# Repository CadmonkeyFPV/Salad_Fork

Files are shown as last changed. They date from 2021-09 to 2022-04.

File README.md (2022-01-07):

# Salad Fork

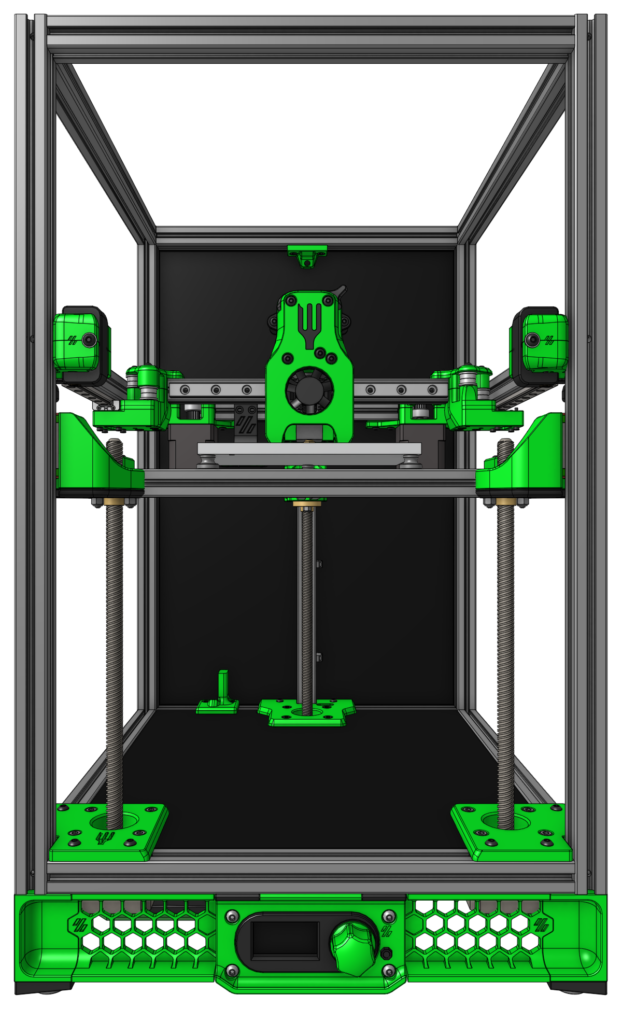
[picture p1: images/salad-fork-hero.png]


The Salad Fork is a [Voron Trident][tridentURL] scaled down to use 1515 aluminum extrusions for the frame instead of 2020, exactly [like how the Micron][micronURL] is a [Voron 2.4][v2URL] scaled down. It is not a modification for a Voron V0, but a from-scratch build that requires longer extrusions and rails, two more V0.1 integrated-leadscrew Z motors, a higher-wattage power supply, possibly a bigger bed…

Why go to the trouble of a whole new build? Well, Salad Fork features:

- Support for build volumes of 120mm³ or 150mm³ (1.95× the build volume of a V0.1!)
- [Klicky support][klickyURL]
- [Purge bucket support][purgeBucketURL]

Coming soon™…

- [Sexbolt support][sexboltURL]
- Magnetically-attached panels

[tridentURL]: https://vorondesign.com/voron_trident
[micronURL]: https://github.com/hartk1213/micron
[v2URL]: https://vorondesign.com/voron2.4
[klickyURL]: https://github.com/jlas1/Klicky-Probe
[purgeBucketURL]: https://github.com/CadmonkeyFPV/Salad_Fork/tree/master/MODS/Dishwasher
[sexboltURL]: https://github.com/hartk1213/MISC/tree/main/Voron%20Mods/Voron%202/2.4/Voron2.4_SexBolt_ZEndstop

# BOM

[The latest official BOM is available on Google Sheets](https://docs.google.com/spreadsheets/d/1IUI6oiu36kkzXx5OPMRfrHjvIH2P_M3332lTih6h6LI/edit#gid=1896851909). The information below may not be complete; last updated November 17, 2021.

<details>
    <summary>
    Frame (120mm³ build volume)
    </summary>

Component | Quantity | Notes
--- | :-: | ---
HFS3-1515-400 | 4 | Cross-drill 7.5mm from both ends, plus drill 1× gantry hole each per drill guide
HFS3-1515-270 | 6 | Tap both ends
HFS3-1515-240 | 5 | Tap both ends, cross-drill 2 extrusions at center
HFS3-1515-230 | 1 | Tap one end
HFS3-1515-210 | 1 |
HFS3-1515-145 | 1 |
HFS3-1515-140 | 1 | Tap one end
</details>

<details>
    <summary>
    Frame (150mm³ build volume)
    </summary>

Component | Quantity | Notes
--- | :-: | ---
HFS3-1515-400 | 4 | Cross-drill 7.5mm from both ends, plus drill 1× gantry hole each per drill guide
HFS3-1515-300 | 6 | Tap both ends
HFS3-1515-270 | 5 | Tap both ends, cross-drill 2 extrusions at center
HSF3-1515-240 | 1 | Tap one end
HSF3-1515-230 | 1 |
HFS3-1515-175 | 1 |
HSF3-1515-170 | 1 | Tap one end
</details>

<details>
    <summary>
    Fasteners
    </summary>

Component | Quantity
--- | :-:
M2x6 BHCS | 24
M2x10 self-tapping | 4
M2x12 SHCS | 8
M3x6 BHCS | 49
M3x6 SHCS | 10
M3x8 BHCS | 41
M3x8 SHCS | 8
M3x10 BHCS | 40
M3x12 BHCS | 4
M3x12 SHCS | 18
M3x16 SHCS | 3
M3x20 SHCS | 6
M3x25 BHCS | 18
M3x25 SHCS | 6
M3x30 BHCS | 2
M3x35 BHCS | 5
M3x35 SHCS | 4
M5x16 BHCS | 3
M3 Heatset | 30
M3 Washer | 26
M3 lock nut | 6
M3 hex nut | 98
M4 knurled nut | 3
M5 hex nut | 3 
6x3 neodymium magnet | 8
</details>

<details>
    <summary>
    Motion
    </summary>

Component | Quantity
--- | :-:
NEMA14 stepper | 2
NEMA17 integrated-leadscrew stepper | 3
MGN9C 180 | 1 (for 120mm³)
MGN7H 200 | 5 (for 120mm³)
MGN9C 210 | 1 (for 150mm³)
MGN7H 230 | 2 (for 150mm³)
MGN7H 200 | 3 (for 150mm³)
Gates GT2 6mm open belt | 4m
F623-RS flanged bearings | 24
GE5C spherical bearings | 3
D2F switch | 4
TR8×8 leadscrew nut | 3
Rubber foot | 4
</details>

<details>
    <summary>
    Electronics
    </summary>

Component | Quantity | Notes
--- | :-: | ---
Control board | 1 | Fysetc Spider or BigTreeTech Octopus
TMC 2209 driver | 6 |
Raspberry Pi | 1 | The Klipper host
C13 power cable | 1 | 
Meanwell UHP-200-24 | 1 |
Keenovo 100mm² 60W 24V heater | 1 | DC bed heater, 120mm³ build
Keenovo 120mm² 120W 24V heater | 1 | DC bed heater, 150mm³ build
Keenovo 100mm² 60W 120/240V heater | 1 | AC bed heater, 120mm³ build
Keenovo 120mm² 120W 120/240V heater | 1 | AC bed heater, 150mm³ build
AC SSR (Omron G3NA-210B-UTU DC5-24, Panasonic AQA211VL) | 1 | for AC bed heater
</details>

<details>
    <summary>
    Toolhead
    </summary>

Component | Quantity | Notes
--- | :-: | ---
NEMA14 pancake stepper | 1 |
BMG gear set | 1 |
3010 axial fan | 1 | Only for Dragonfly BMS hotend
3007 axial fan | 1 | All other hotends
3010 blower fan | 2 |
Hotend | 1 |
</details>

# Salad Fork in action

Salad Fork video from CadmonkeyFPV (https://youtu.be/ibptF2t73A4)

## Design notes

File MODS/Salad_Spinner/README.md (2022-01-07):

# The Salad Spinner Spool Holder

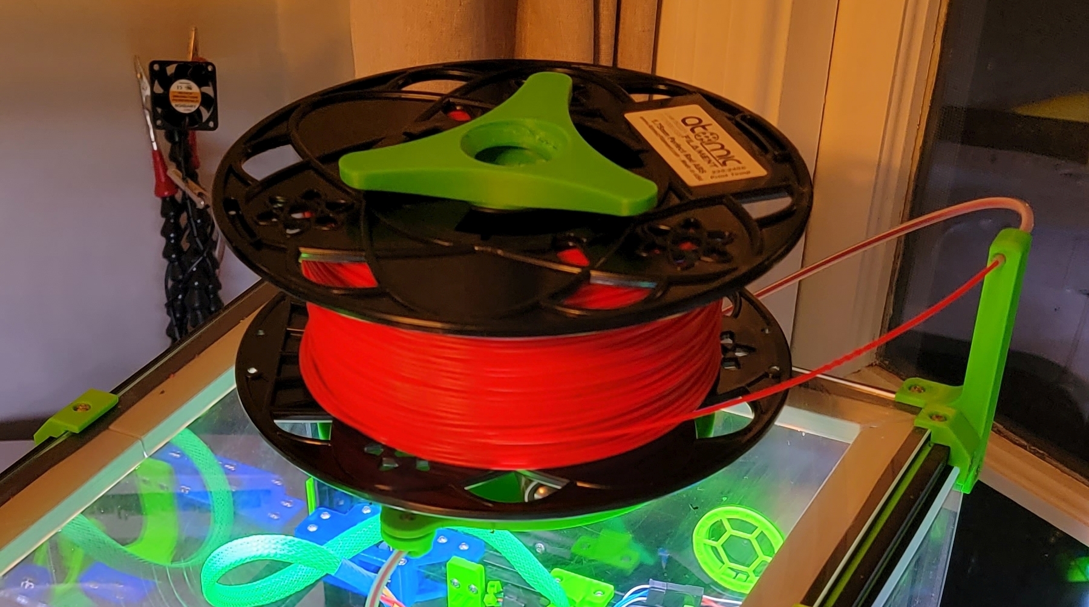
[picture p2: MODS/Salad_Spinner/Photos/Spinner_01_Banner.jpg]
The Salad Spinner


Horizontal Spool Holder designed for the Salad Fork project but adaptable to many other printers.

Intended to mount to top panel of printer. Stand alone turntable for use on other platforms.

Threaded clamps for 1kg and 5 pound spools (5 pound version has only been tested on KVP 5 pound spool at this time) and a clamp for thinner spools (0.25 kg SainSmart TPU for example)

Turntable gets mounted to top panel of printer. Rectangular boss achors to rear of printer and riser couples that to extrusion using M3x12 BHCS and preloaded hex nut. Adjust riser Z dimension in slicer to accomodate different panel and foam combinations, STL as provided works with 3mm panel, 6mm foam compressed to 5mm. The front ear on the turntable requires the top panel to be drilled to accept an M3, and the Bowden guide (with heat set installed) mounts to the interior of the printer on this bolt. Guide loosely secures the Bowden mid span. You will need to experiment with overall bowden length to determine was works best for your toolhead and other accessories/mods. I have enough Bowden to extend 4" past the front panel when stretched out, which coils down to the Orbiter I am running.

Standalone Turntable uses (3) M3 BHCS sized to work with your panel thickness.

Spinner core gets M5 heat set inserts in each leg. Follow that with a flat washer or shim against the body, one bearing and finally secure with an M5x12 BHCS. Repeat 2 more times for each leg.

Corner Clip Bowden support mounts replaces the top panel corner mount and supports the spool end of the reverse Bowden tube at approx middle of the spool. Bowden is a tight fit, use a rat tail file if you need to open up bore to get the tube in place. There is a bend in the bore to help hold this tight.

## BOM - Per spinner Core

- (3) M5x12 BHCS (SHCS should work as well)
- (3) M5 Heat Set Inserts [Amazon](https://www.amazon.com/gp/product/B07NBSWBQ8)
- (3) M5 flat washers or 5mm x 1mm shims
- (3) 625 bearings - any variant can be used - RS, ZZ, etc

## BOM - Turntable Salad Fork w/ 3mm acrylic top panel

- (1) M3x8 BHCS 
- (1) M3x12 BHCS (or M3x10)
- (1) M3 Hex Nut
- (1) M3 Short Heat Set Insert (Voron Standard)

### OPTIONAL BOM - Bowden BPST - Secures Bowden tube where it passes through rear panel into the print cavity

- (1) Pass through Bowden BPST fitting

### OPTIONAL BOM - Turntable Standalone - For use on other printers (I'm using on a V2.4)

- (3) M3 BHCS - Length appropriate for panel thickness

#### Coming Soon - "Top Hat" style 1515 extrusion based cover for Salad Forks

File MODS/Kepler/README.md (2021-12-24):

# Kepler Tool Head

Derived from the Micron and Mini-Afterburner Tool Heads

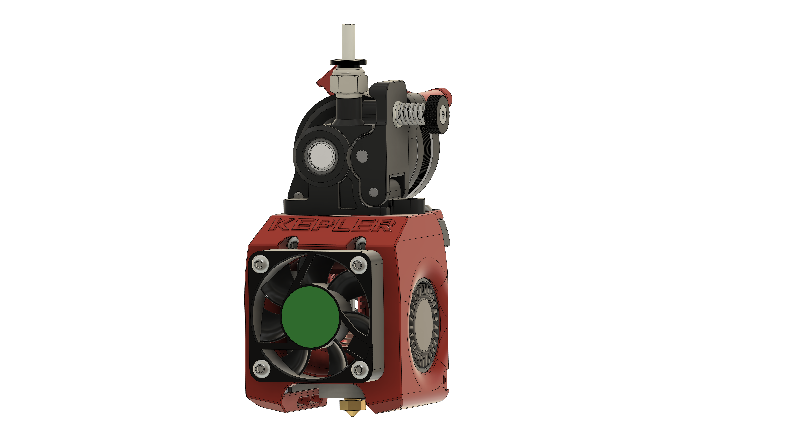
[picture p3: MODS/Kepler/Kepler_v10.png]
Kepler


# Use at your own risk - this is still a work in progress.

I'm running this on a Salad Fork build. Better overhang results and extrusion consistency so far as compared to the Micron toolhead.

This only supports the Dragon Hot End at this time

## BOM

- (1) Orbiter v1.5
- (1) Dragon Hot End - Standard or Hi-Flow variants
- (1) Pancake Stepper Toolhead PCB
- (2) 4010 Radial Fans - whatever voltage you prefer
- (1) 4010 Axial Fan - whatever voltage you prefer
- (4) M3x10 BHCS Hot End Fan
- (4) M3 Hexnuts Hot End Fan
- (2) M3x35 SHCS Main Mounting Screws
- (1) M3x6 3rd Mounting Point
- (4) M3x8 BHCS Carriage Mount
- (2) M3x20 SHCS Klicky Mount
- (2) M3x10 BHCS Blower Anchors (optional?)
- (2) M3x10 BHCS Orbiter Mount
- (2) M3x6 PCB Anchors
- (4) M2.5x?? The Dragon Screws for a v0
- Zip Ties to keep it neat

Assembly Tips:
- Remove the upper ears on the 4010 Radials
- Insert the (2) M3x35 SHCS before installing the Hot End Fan
- Route the Hot End Fan wires down and through the fan hole, merge with the 4010 Radial Fan through the nut channel
- Assemble the Hot End Fan before the Radials, the nuts will be mostly captivated once the 4010 Radials are inserted
- Be mindful of the wires - the loops are enough for the part fans, thermocouple, and Hot End Fan.
- Heater wires hang loose at this stage, zip tie to the secured fan wires to keep them from dangling

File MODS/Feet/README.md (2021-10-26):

# TPU Feet

Alternate feet for the Salad Fork

Foot Model

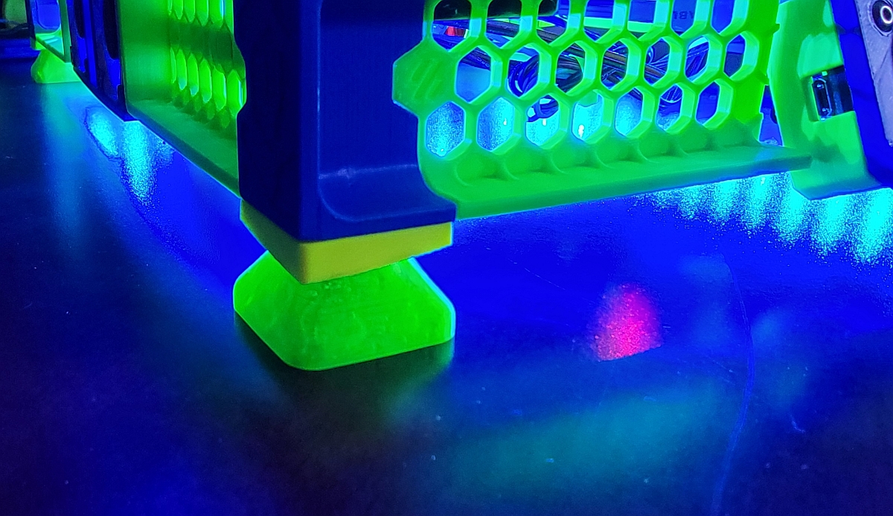
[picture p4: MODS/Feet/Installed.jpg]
Installed


Print in TPU - Low wall count ~2 and minimal infill ~10% gyroid worked well for me to yield a supple foot with some vibration isolation, 5 top/bottom layers

## BOM
- (4) M3x10 SHCS

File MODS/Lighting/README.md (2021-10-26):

# Light Bar Mounts 

For 12mm wide LED strips

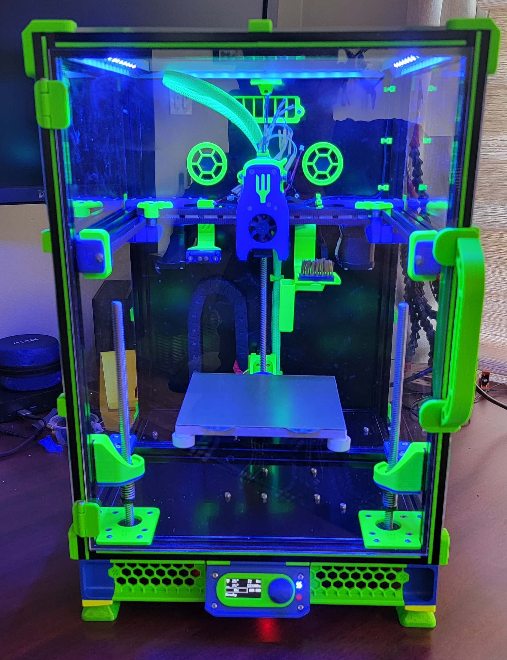
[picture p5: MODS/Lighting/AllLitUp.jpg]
All Liut Up


Print sections per your frame size. Parametric Fusion360 file provided to customize lengths

## BOM

- (2) M3x6 BHCS per segment
- (2) M3 Hexnuts per segment
- 12mm wide (or less) LED strip

Assembly is straightforward.

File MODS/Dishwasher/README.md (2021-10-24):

# The "Dishwasher" Nozzle Scrubber and Purge Bucket

Nozzle scrubber and purge bucket designed for the Salad Fork project.

Bolts to underside of rear 1515 extrusion, adjacent to A Drive

Spacing based on Mini-Afterburner with Dragon Hotend

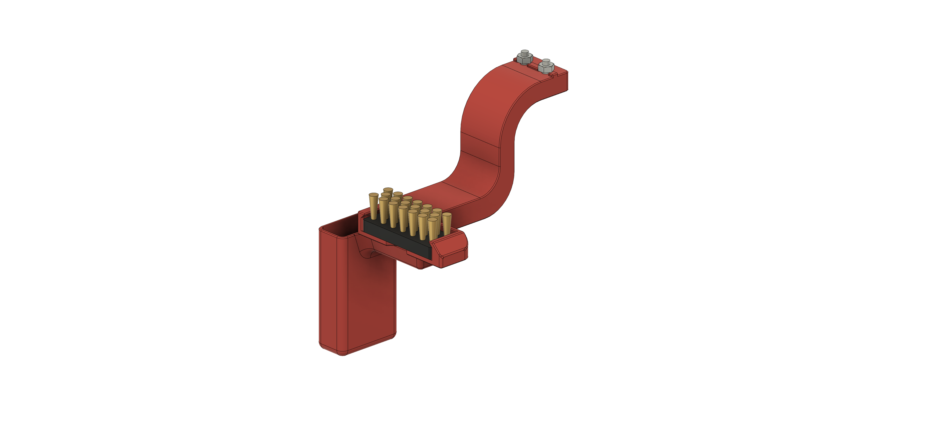
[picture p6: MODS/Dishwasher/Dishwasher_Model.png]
The Dishwasher

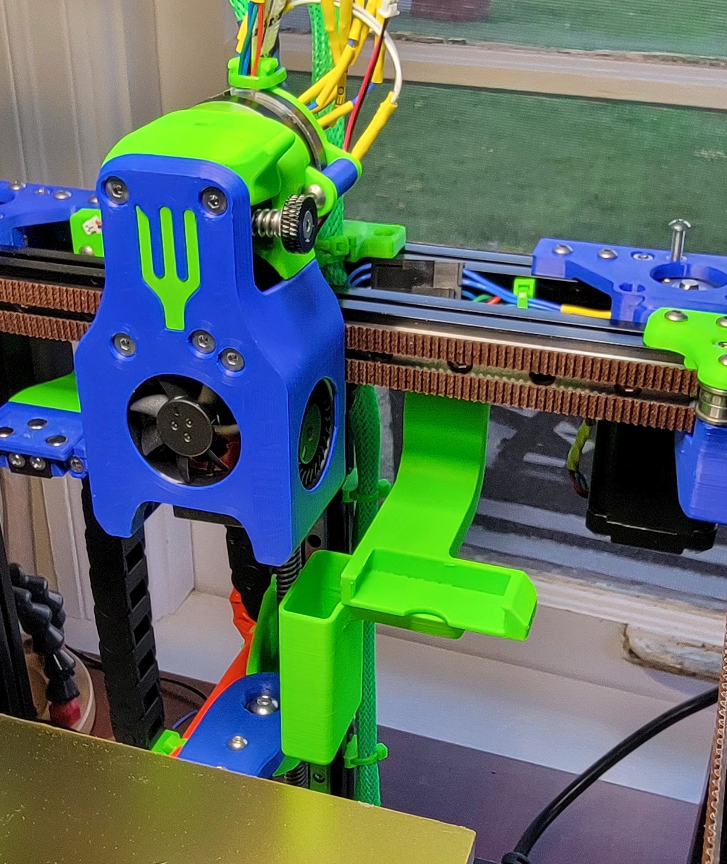
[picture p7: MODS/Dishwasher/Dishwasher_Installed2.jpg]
Installed


## BOM

- (2) M3x10 SHCS
- (2) M3 Hexnuts
- (6) 6x3 Magnets
- (1) Brass Mini-Brush (cut head off)

Brush overall height (head & bristles) should be roughly 15mm

Assembly is straightforward.

20211023 - Additional STL for +8mm drop on the mount to accomodate longer bristles of Home Depot brushes

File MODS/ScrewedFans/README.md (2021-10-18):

# Fan Supports with M3 Screw Tabs

Upgraded fan support for the Salad Fork project. 

Provides tabs to screw the 4010 electronics bay fans in place. M3 SHCS threads into the plastic, no heat set required.

The Dishwasher
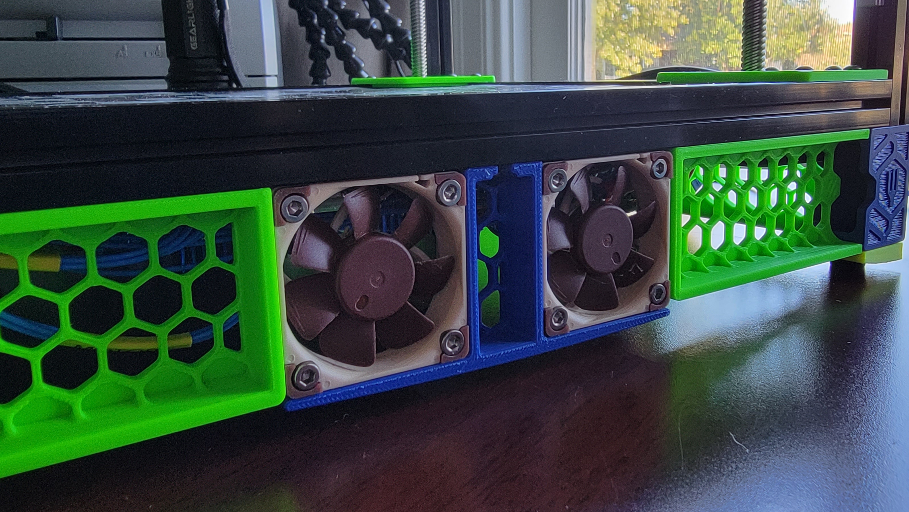
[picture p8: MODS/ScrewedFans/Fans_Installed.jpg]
Installed


## BOM

- (6) M3x12 SHCS
- (2) 4010 Fans (I prefer Noctua for whisper quiet silence)
- (1) M3x6 BHCS (to mount to extrusion if you don't already have)
- (1) M3 Hex Nut (ditto)

Press firmly as you thread the screws in so they form some amount of thread instead of just cutting plastic out of the way.

I added (2) additional M3x12 w/ hexnuts in the unsupported corner just for aesthetics. They aren't required though.

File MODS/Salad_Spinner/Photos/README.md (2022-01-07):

# The Salad Spinner Spool Holder

### Overview
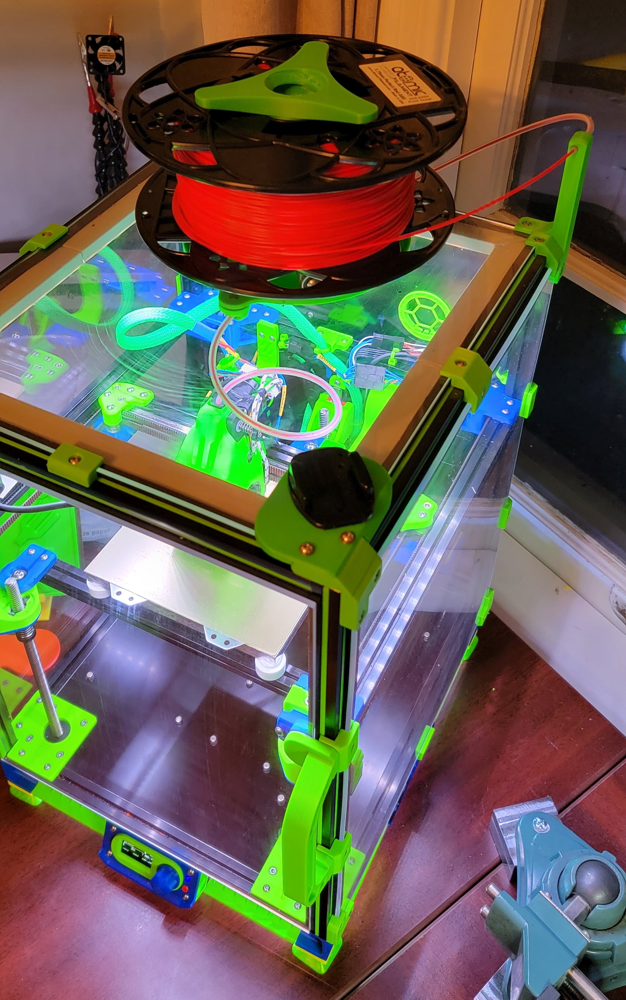
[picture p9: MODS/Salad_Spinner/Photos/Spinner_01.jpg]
Overview


### Turntable
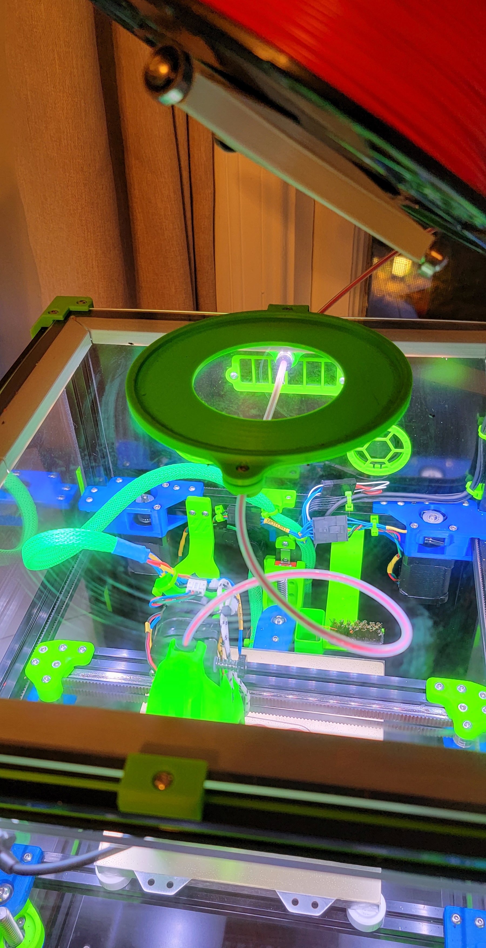
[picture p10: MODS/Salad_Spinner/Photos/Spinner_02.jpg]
Turntable


### Bowden Routing
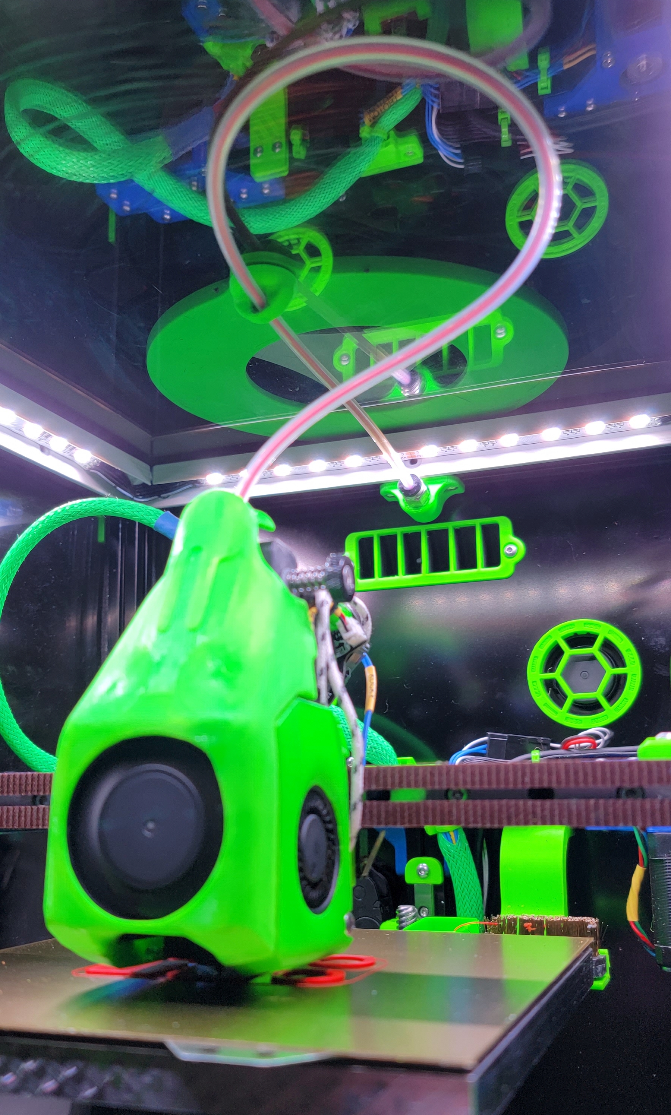
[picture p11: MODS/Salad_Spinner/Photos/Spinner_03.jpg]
Bowden


### Stable of Spinners
Stable

### Spinner Detail 1
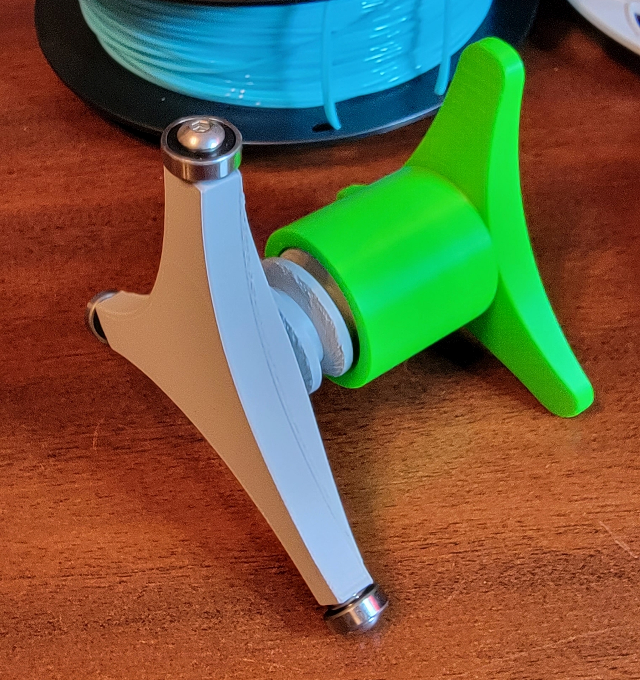
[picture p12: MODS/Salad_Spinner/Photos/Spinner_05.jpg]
Detail1


### Spinner Detail 2
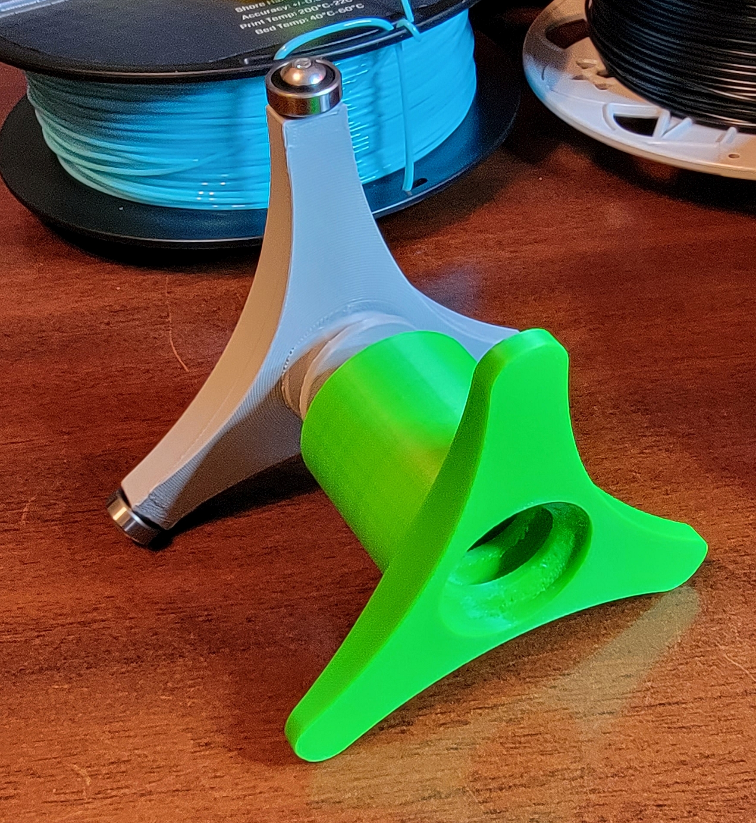
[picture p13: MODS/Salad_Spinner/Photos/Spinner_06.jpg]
Detail2


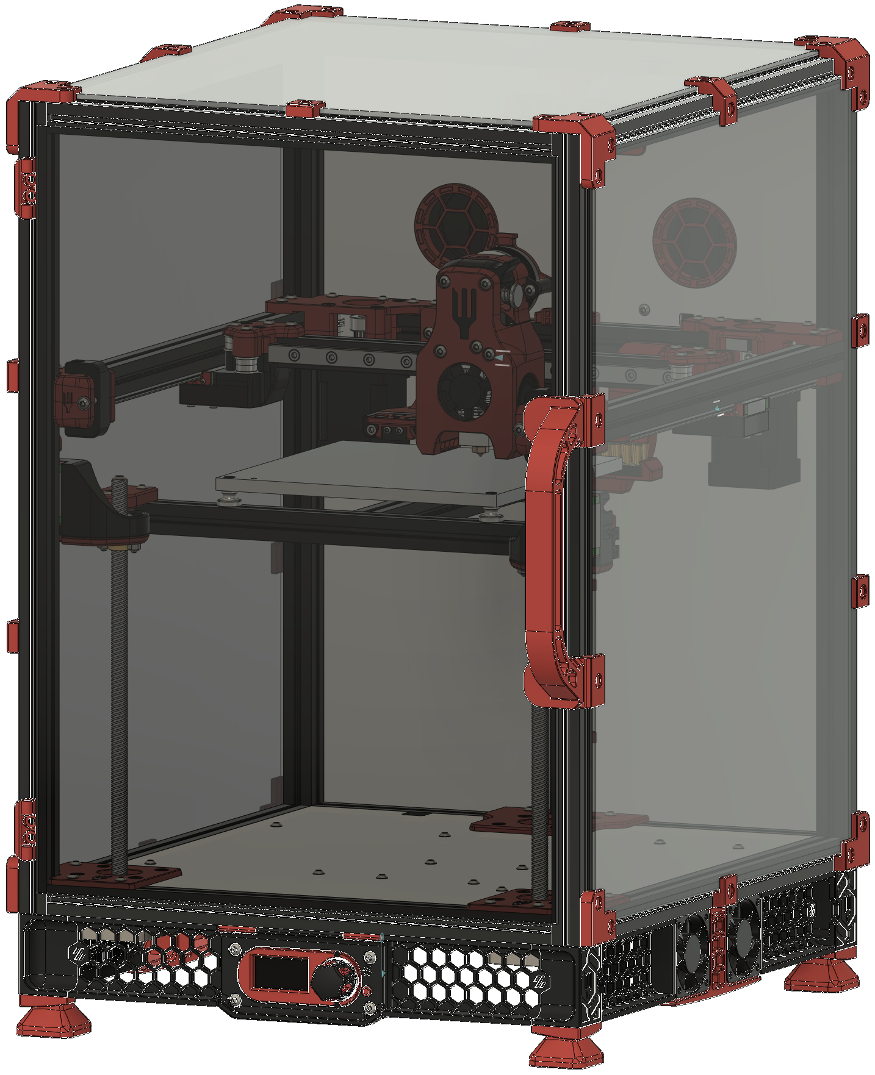
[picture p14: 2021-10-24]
Images/SF_Assy_20190919_v21.png

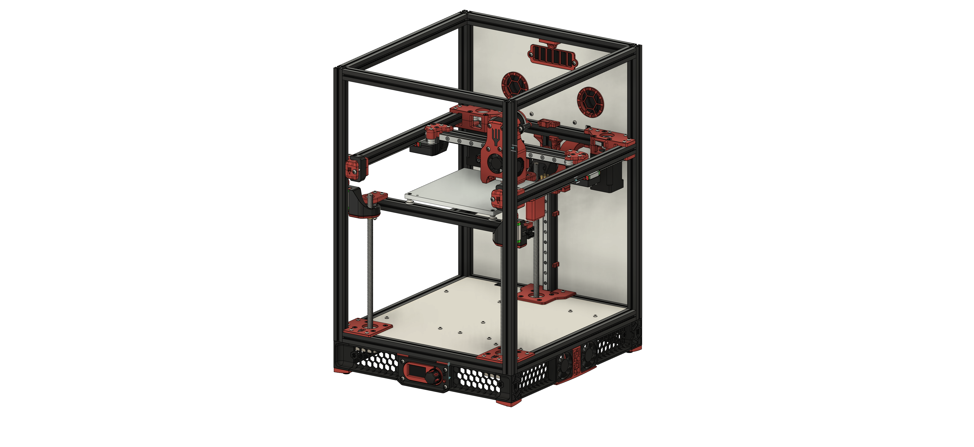
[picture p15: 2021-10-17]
Images/Salad_Fork_CADMonkeyFPV.png

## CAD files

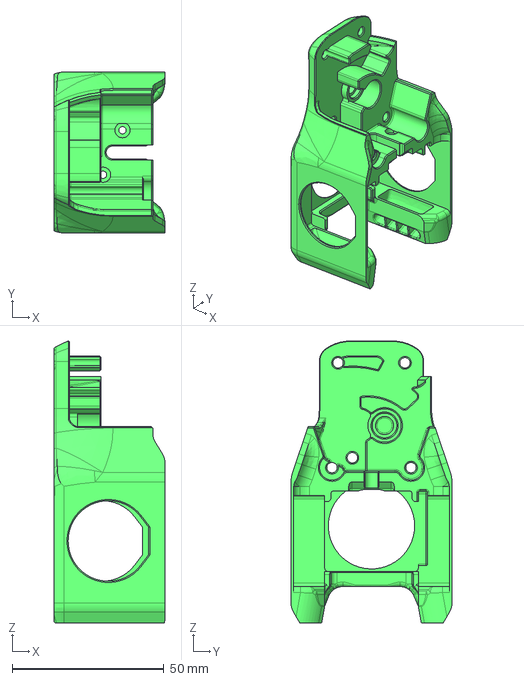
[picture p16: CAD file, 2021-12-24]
CAD/Cowling_Dragonfly_BMO.step
36.5 x 53.0 x 92.8 mm

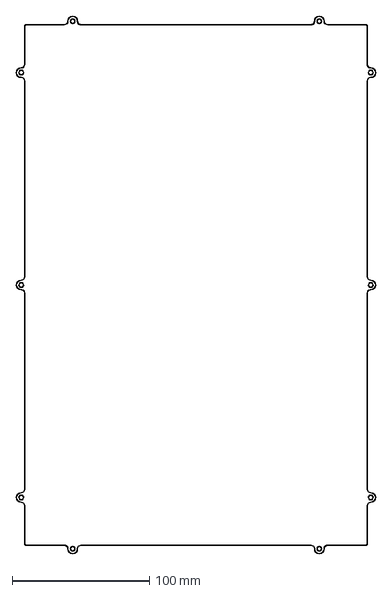
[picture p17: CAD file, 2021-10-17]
DXF/120/back.dxf
262.0 x 391.9 mm

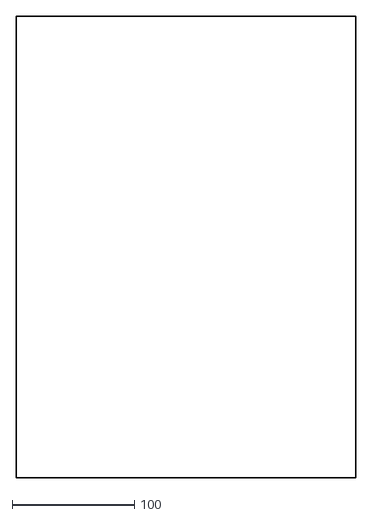
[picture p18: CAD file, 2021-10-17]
DXF/CADMonkeys_DXFs/ACRYLIC_FRONT_CLEAR_x1.dxf
278.0 x 378.0

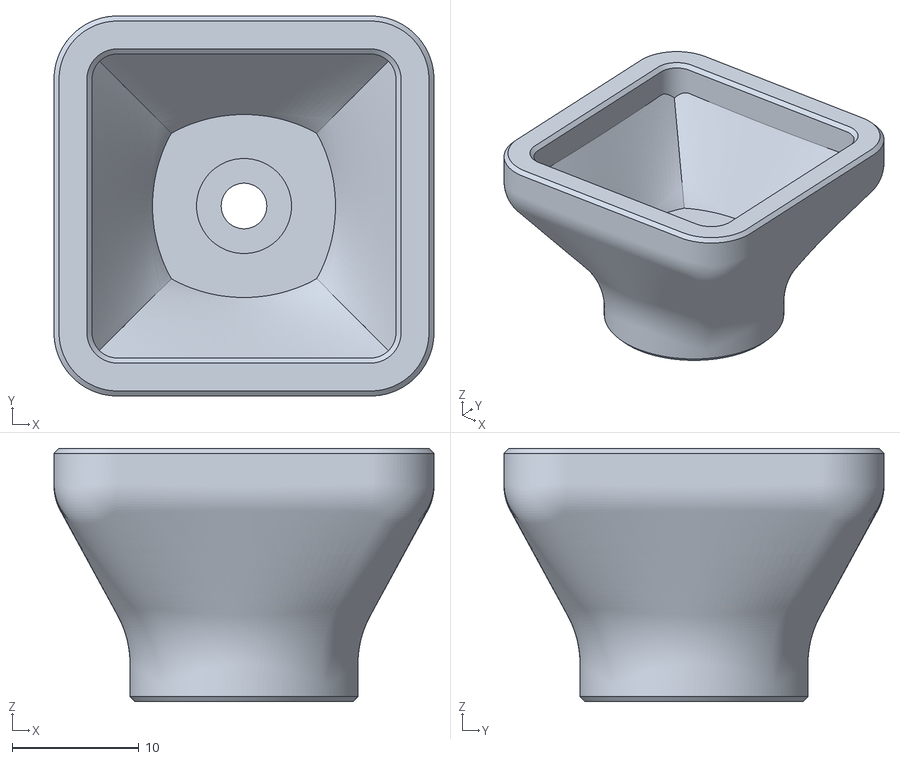
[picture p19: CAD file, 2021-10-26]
MODS/Feet/[a]_TPU_Foot_x4.stl
30.0 x 30.0 x 20.0

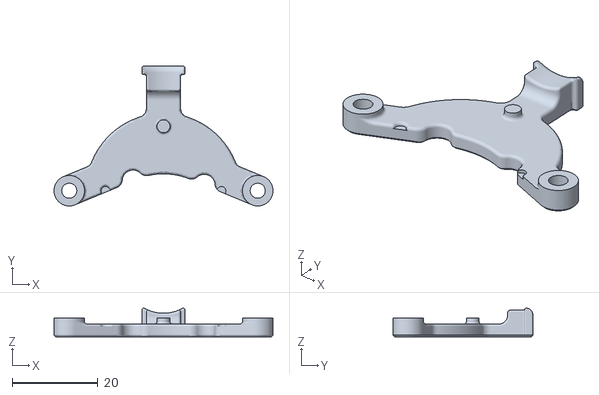
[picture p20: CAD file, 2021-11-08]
MODS/Kepler/Kepler_Strain_Relief_v3.stl
50.9 x 32.5 x 6.69

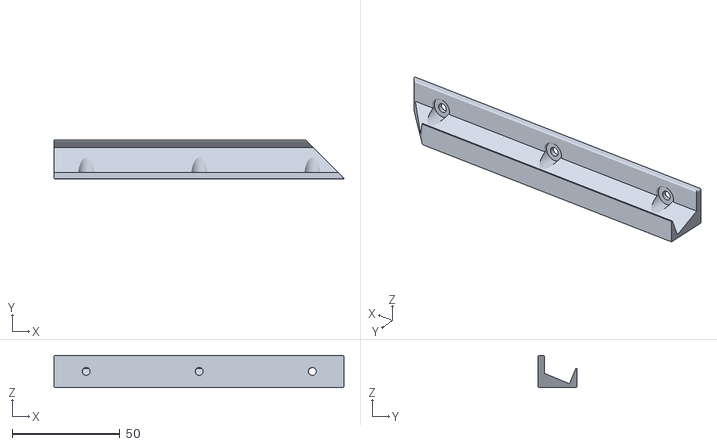
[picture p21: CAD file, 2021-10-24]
MODS/Lighting/LightBar_135B_v1.stl
134.6 x 18.0 x 15.0

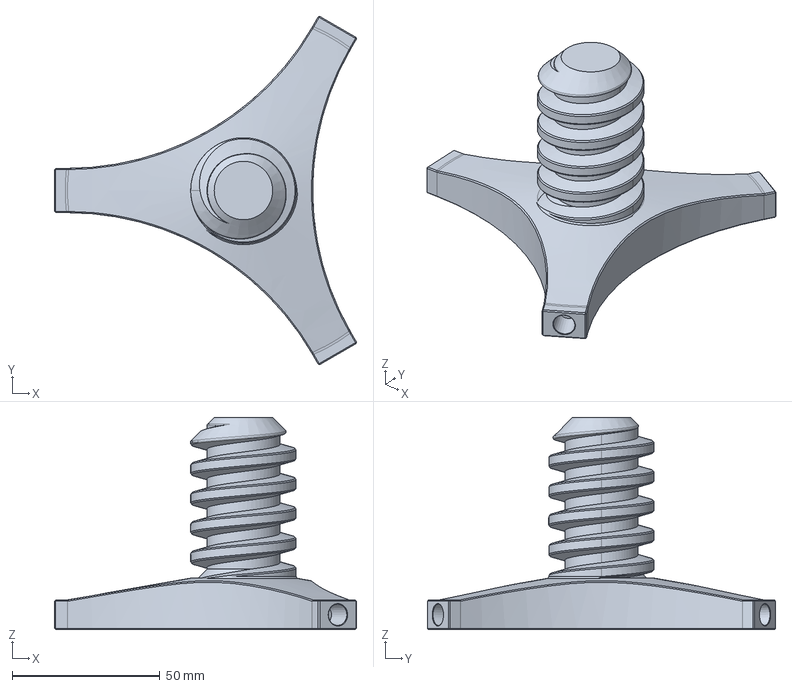
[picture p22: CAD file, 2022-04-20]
MODS/Salad_Spinner/CAD/Filament_Spinner_7.1ODInserts.step
102.3 x 118.0 x 71.9 mm

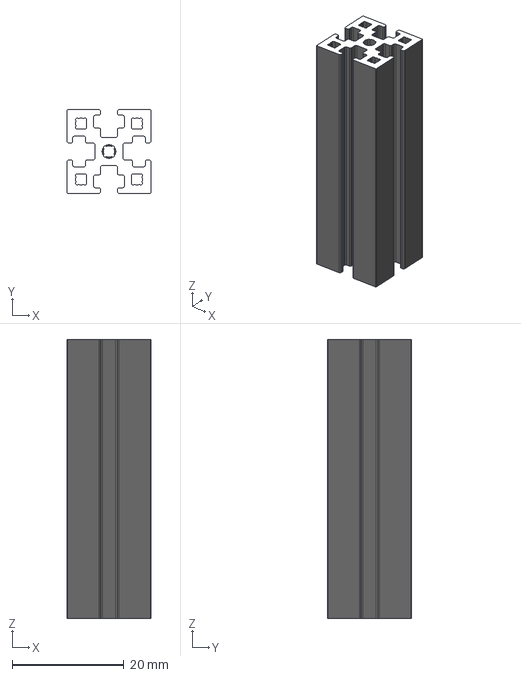
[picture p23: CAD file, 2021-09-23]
References/MakerBeam1515.stp
15.0 x 15.0 x 50.0 mm

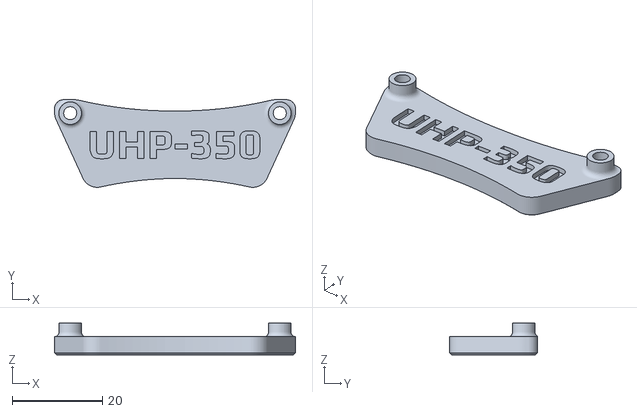
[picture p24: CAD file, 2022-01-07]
STL/Electronics/UHP-350_bracket_x2.stl
53.4 x 19.4 x 7.00

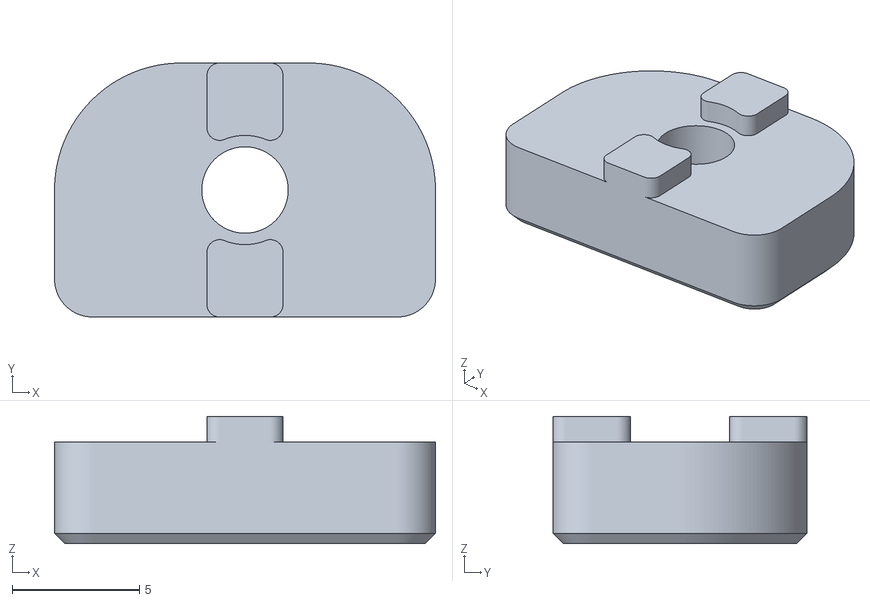
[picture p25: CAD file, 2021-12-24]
STL/Frame/[a]_railstop_x5.stl
15.0 x 10.0 x 5.00

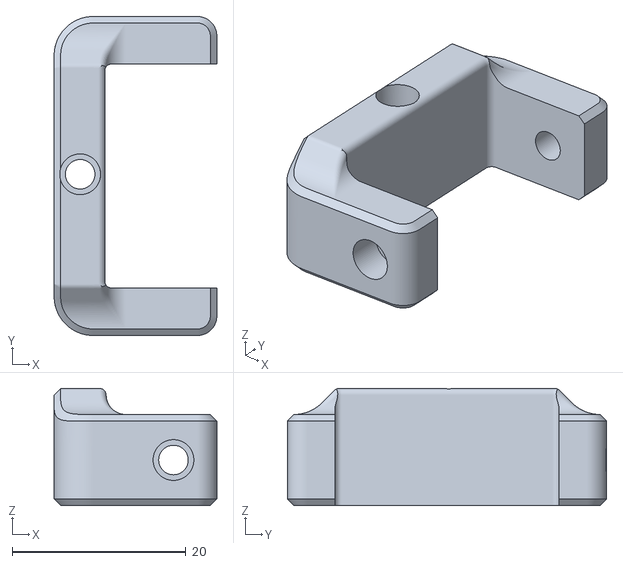
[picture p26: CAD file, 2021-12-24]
STL/Gantry/[a]_tensioner_b_x1.stl
18.8 x 36.8 x 13.5

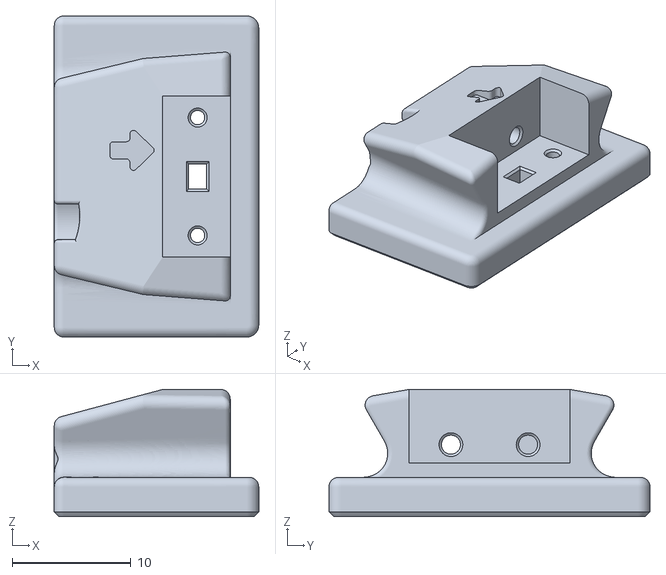
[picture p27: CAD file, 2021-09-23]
STL/Klicky/probe_body_x1.stl
17.2 x 27.0 x 10.7

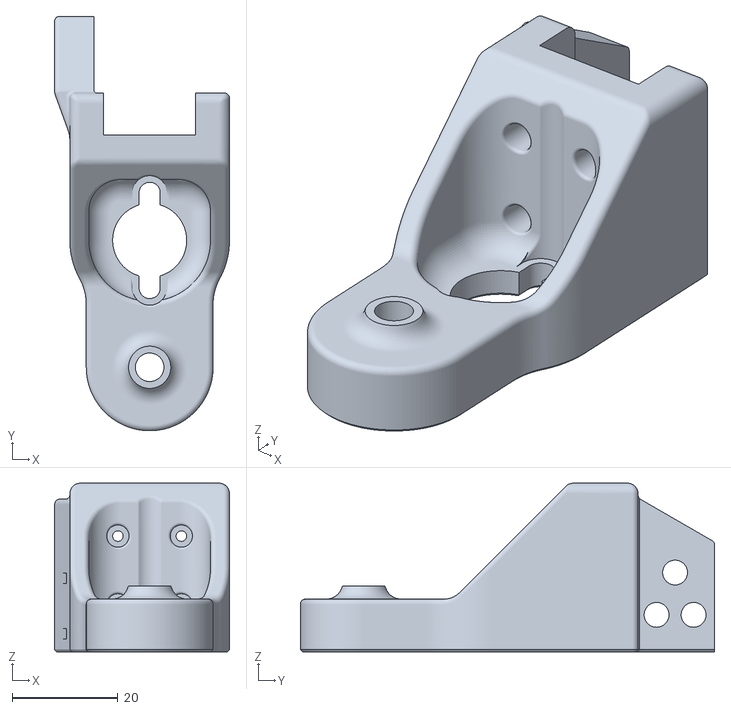
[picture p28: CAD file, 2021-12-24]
STL/Motion/z_carriage_rear_3hole_x1.stl
33.1 x 78.4 x 31.9

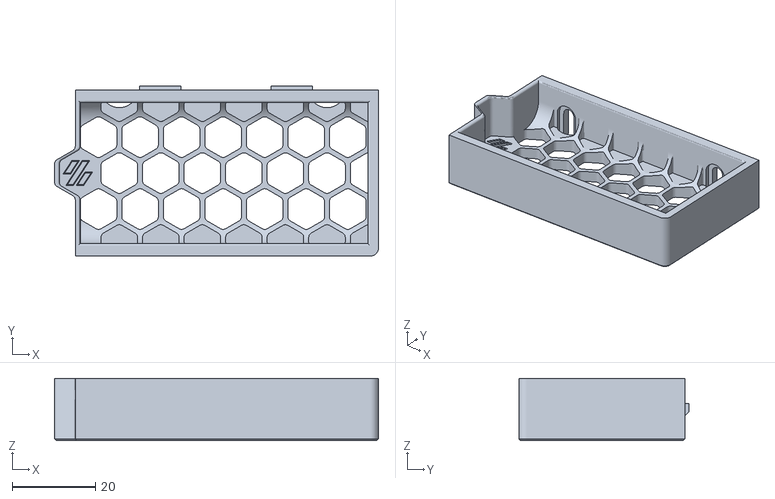
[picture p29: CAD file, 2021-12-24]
STL/Skirts/120/Skirt_Side_B_120_x2.stl
78.0 x 41.0 x 15.0

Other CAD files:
DXF/150/back_recover.dwg
MODS/Salad_Spinner/Spinner_Core_7.1ODInserts.stl
STL/Skirts/150/Skirt_Side_B_150_x2.stl
STL/Skirts/display/[a]_stop_button_x1.stl
DXF/120/deck.dxf
DXF/150/back.dxf
DXF/150/clees-back.dxf
DXF/150/deck.dxf
DXF/150/deck_recover.dwg
DXF/CADMonkeys_DXFs/ACM_DECK_WHITE_x1.dxf
DXF/CADMonkeys_DXFs/ACM_REAR_WHITE_x1.dxf
DXF/CADMonkeys_DXFs/ACRYLIC_SIDES_CLEAR_x2.dxf
DXF/CADMonkeys_DXFs/ACRYLIC_TOP_CLEAR_x1.dxf
MODS/Dishwasher/Dishwasher_Assy v4.step
MODS/Dishwasher/Dishwasher_Brush_Holder+8mmHD.stl
MODS/Dishwasher/Dishwasher_Brush_Holder_x1.stl
MODS/Dishwasher/Dishwasher_Bucket_Taller_v1.stl
MODS/Dishwasher/Dishwasher_Bucket_x1.stl
MODS/Kepler/Carriage_Kepler_v19.stl
MODS/Kepler/Kepler_HotEnd_v10.stl
MODS/Kepler/Spacers_x2.stl
MODS/Lighting/LightBar_135A_v1.stl
MODS/Lighting/LightBar_150A_v1.stl
MODS/Lighting/LightBar_150B_v1.stl
MODS/Lighting/LightBar_270_v1.stl
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

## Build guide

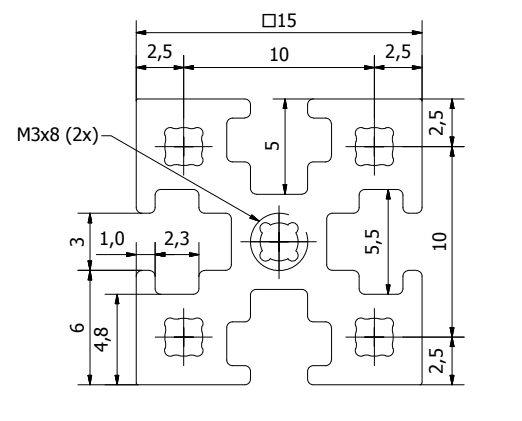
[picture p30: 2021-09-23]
References/MakerBeam 1515.png

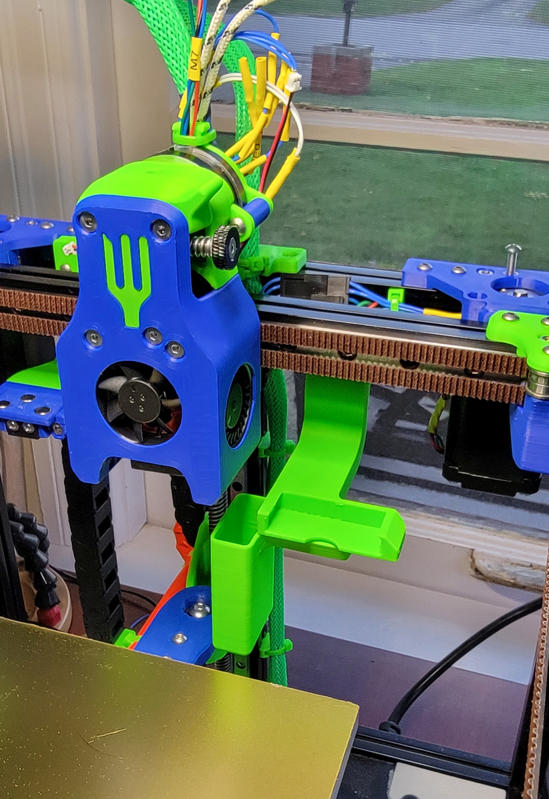
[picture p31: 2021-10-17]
MODS/Dishwasher/Dishwasher_Installed.jpg

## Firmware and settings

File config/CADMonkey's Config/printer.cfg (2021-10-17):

# INCLUDES
[include TMC2209.cfg]
#[include input_shaper.cfg]
[include mainsail.cfg]
[include macros.cfg]
[include klicky_sf.cfg]
[include DisplayEncoder.cfg]

[duplicate_pin_override]
pins: mcu_temp, ADC_TEMPERATURE, PF5

# INTERFACE
[mcu]
serial: /dev/ttyAMA0
restart_method: command
baud: 250000

[printer]
kinematics: corexy
max_velocity: 600  
max_accel: 5000
max_z_velocity: 5
max_z_accel: 100
square_corner_velocity: 5.0  

#####################################################################
## 	                   X/Y Stepper Settings                        ##
#####################################################################

######################
# X motor - Driver 1 #
######################

[stepper_x]
step_pin: PG0
dir_pin: PG1
enable_pin: !PF15
rotation_distance: 32
full_steps_per_rotation: 200
microsteps: 16
endstop_pin: ^PG6 #J27 - DIAG0
position_min: -25

##	Uncomment below for 120mm build
#position_endstop: 120
#position_max: 120

##	Uncomment for 150mm build
position_endstop: 155
position_max: 175

homing_speed: 75   #Max 100
homing_retract_dist: 5
homing_retract_speed: 20
second_homing_speed: 10
homing_positive_dir: true

######################
# Y motor - Driver 0 #
######################

[stepper_y]
step_pin: PF13
dir_pin: !PF12
enable_pin: !PF14
#step_distance: 0.0125
rotation_distance: 32
microsteps: 16
full_steps_per_rotation: 200
endstop_pin: ^PG9 #J29 - DIAG1
position_min: -33

##	Uncomment for 120mm build
#position_endstop: 120
#position_max: 120

##	Uncomment for 150mm build
position_endstop: 172
position_max: 192

homing_speed: 75  #Max 100
homing_retract_dist: 5
homing_retract_speed: 20
second_homing_speed: 10
homing_positive_dir: true

######################################
# Z0 Stepper - Left Front - Driver 3 #
######################################

## T8x8 Lead Screws.  One rotation moves the bed 8mm 
## Change according to integrated steppers purchased

[stepper_z]
step_pin: PG4
dir_pin: !PC1
enable_pin: !PA0
rotation_distance: 8
full_steps_per_rotation: 200
microsteps: 16
endstop_pin: probe:z_virtual_endstop

#  Z-position of nozzle (in mm) to z-endstop trigger point relative to print surface (Z0)
#  (+) value = endstop above Z0, (-) value = endstop below
#  Increasing position_endstop brings nozzle closer to the bed
#  After you run Z_ENDSTOP_CALIBRATE, position_endstop will be stored at the very end of your config

#position_endstop: -0.5

## All builds use same Max Z
position_max: 250

position_min: -5
homing_speed: 8 # VERIFY
second_homing_speed: 3.0
homing_retract_dist: 3.0

#######################################
# Z1 Stepper - Rear Center - Driver 4 #
#######################################

## T8x8 Lead Screws.  One rotation moves the bed 8mm 
## Change according to integrated steppers purchased

[stepper_z1]
step_pin: PF9
dir_pin: !PF10
enable_pin: !PG2
rotation_distance: 8
full_steps_per_rotation: 200
microsteps: 16

#######################################
# Z2 Stepper - Front Right - Driver 5 #
#######################################

## T8x8 Lead Screws.  One rotation moves the bed 8mm 
## Change according to integrated steppers purchased

[stepper_z2]
step_pin: PC13
dir_pin: PF0
enable_pin: !PF1
rotation_distance: 8
full_steps_per_rotation: 200
microsteps: 16

#########################
# Extruder 0 - Driver 7 #
#########################

# Tune per individual printer
# Default for Bondtech 5mm Bore Drive Gears

[extruder]
step_pin: PE6
dir_pin: PA14
enable_pin: !PE0
rotation_distance: 22.6789511
gear_ratio: 50:17
microsteps: 16
full_steps_per_rotation: 200
nozzle_diameter: 0.400
filament_diameter: 1.75
heater_pin: PA2 # HE0
##	Validate the following thermistor type to make sure it is correct
sensor_type: NTC 100K beta 3950
sensor_pin: PF4 #J45
min_temp: 10
max_temp: 270
max_power: 1.0
min_extrude_temp: 170
control = pid
## RUN 'PID_CALIBRATE HEATER=extruder TARGET=240' DURING COMMISSIONING (ADJUST TARGET TEMPERATURE TO MATCH FILAMENT)
pid_Kp: 28.182
pid_Ki: 1.978
pid_Kd: 100.397
## Set appropriate once tuning your printer ##
#pressure_advance: .05
##	Default smooth time is 0.040, leave stock
pressure_advance_smooth_time: 0.040
max_extrude_only_distance: 200.0

########################
# Bed Heater - BED_OUT #
########################

[heater_bed]
heater_pin: PA1

##  Choose the correct thermistor for your heater
sensor_type: NTC 100K beta 3950 # For Keenovo, verify yours

sensor_pin: PF3
#max_power: 0.6			# ONLY NEEDED FOR 100W BEDS
smooth_time: 3.0
min_temp: 0
max_temp: 120
#control: pid
## RUN 'PID_CALIBRATE HEATER=heater_bed TARGET=110' DURING COMMISSIONING (ADJUST TARGET TEMPERATURE TO MATCH FILAMENT)
#pid_kp: 68.453
#pid_ki: 2.749
#pid_kd: 426.122

#####################################################################
# 	Probe
#####################################################################

################
# Klicky Probe #
################
[probe]
pin: ^PG10  #J31 - DIAG2
x_offset: 1.8353
y_offset: 28.5337
z_offset: 3.8668
speed: 10
samples: 5
samples_result: median
sample_retract_dist: 3
samples_tolerance: 0.006
samples_tolerance_retries: 3

#####################################################################
# FILAMENT RUNOUT SENSOR - OPTIONAL - UNCOMMENT SECTION IF USED     #
#####################################################################

## DIGITAL_IN0
#[filament_switch_sensor material_0]
#switch_pin: !PG12
#pause_on_runout: True
#pause_delay: 0.5

#####################################################################
# 	Fan Control
#####################################################################

#################
#  HOT END FAN  #
#################

[heater_fan extruder_fan]
pin: PA8   #J50/FAN0 - SET J58 TO CORRECT VOLTAGE
heater: extruder
heater_temp: 50.0
##	If you are experiencing back flow, you can reduce fan_speed
#fan_speed: 1.0			# PWM DOES NOT WORK WITH DELTA FAN UNLESS USING THE BLUE WIRE

#################
#   PART FAN    #
#################

[fan]
pin: PE5  #J51/FAN1 - SET J59 TO CORRECT VOLTAGE
cycle_time: 0.010
off_below: 0.13
##	Depending on your fan, you may need to increase this value
##	if your fan will not start. Can change cycle_time (increase)
##	if your fan is not able to slow down effectively
kick_start_time: 0.5

###########################
#  EXHAUST FAN - OPTIONAL #
###########################

#[heater_fan exhaust_fan]
##	Exhaust Fan - Bed Connector (Optional)
#pin: PD12 #J52/FAN2 - SET J60 TO CORRECT VOLTAGE
#max_power: 1.0
#shutdown_speed: 0.0
#kick_start_time: 5.0
#heater: heater_bed
#heater_temp: 60
#fan_speed: 1.0

#####################################################################
# CHAMBER TEMPERATURE SENSOR - OPTIONAL - UNCOMMENT SECTION IF USED #
#####################################################################

#[thermistor chamber_temp]
#temperature1: 25
#resistance1: 10000
#beta: 3950

#[temperature_sensor chamber]
#sensor_type: chamber_temp
#sensor_pin: PF5 #J46/T1
#min_temp: 0
#max_temp: 100
#gcode_id: C

############################################################################
#   HOST & MCU TEMP SENSORS - OPTIONAL - COMMENT OUT SECTION IF NOT USED   #
############################################################################
# REQUIRED FOR TEMPERATURE CONTROLLED FANS CONFIGURED IN FOLLOWING SECTION #
############################################################################

[temperature_sensor _raspberry_pi]
sensor_type: temperature_host
min_temp: 10
max_temp: 100

[temperature_sensor _mcu_temp]
sensor_type: temperature_mcu
min_temp: 0
max_temp: 100

######################################################################
# HOST & MCU COOLING FANS - OPTIONAL - UNCOMMENT SECTION IF NOT USED #
######################################################################


# FAN4 - PI FAN
[temperature_fan _Pi_fan]
pin: PD14 #J54/FAN5 - SET J62 TO CORRECT VOLTAGE
kick_start_time: 1.0
sensor_type: temperature_host
target_temp: 35.0
max_speed: 1.0
min_speed: 0.3
min_temp: 0
max_temp: 100
shutdown_speed: 1.0
control: pid
pid_Kp: 10.000
pid_Ki: 1.000
pid_Kd: 2.000

# FAN5 - MCU FAN
[temperature_fan _MCU_fan]
pin: PD15 #J55/FAN5 - SET J63 TO CORRECT VOLTAGE
kick_start_time: 1.0
sensor_type: temperature_mcu
target_temp: 30.0
max_speed: 1.0
min_speed: 0.3
min_temp: 0
max_temp: 100
shutdown_speed: 1.0
control: pid
pid_Kp: 10.000
pid_Ki: 1.000
pid_Kd: 2.000

#####################################################################
# 	Homing and Tilt Adjustment Routines
#####################################################################

[idle_timeout]
timeout: 1800

# Refer to include: klickysf.cfg for homing_override

[z_tilt]
##	Use Z_TILT_ADJUST to level the bed left to right.
##	z_positions: Location of toolhead

## Uncomment below for 150mm build
z_positions:
	-37.36, -31.77
	75, 219.38
	187.34, -31.77
points:
	10, -5
	75, 111
	140, -5

speed: 200
horizontal_move_z: 10
retries: 5
retry_tolerance: 0.0075
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

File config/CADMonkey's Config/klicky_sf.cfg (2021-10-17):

# This macro was provided by discord user Garrettwp to whom i give my thanks for sharing it with me.
# The v1.8 version template was provided by Yeri, who helped to debug prior to release, thanks again.
# I have tweaked it a lot.
#
# this macro is  based on the great Annex magprobe dockable probe macros "#Originally developed by Mental, modified for better use on K-series printers by RyanG and Trails"
# that macro can be found here https://github.com/Annex-Engineering/Annex-Engineering_Other_Printer_Mods/blob/master/All_Printers/Microswitch_Probe/Klipper_Macros/dockable_probe_macros.cfg
#
# by standing on the shoulders of giants, lets see if we can see further

[gcode_macro User_Variables]
variable_verbose:               True  # Enable verbose output
variable_travel_speed:          200   # how fast all other travel moves will be performed when running these macros
variable_dock_speed:            50    # how fast should the toolhead move when docking the probe for the final movement
variable_release_speed:         100    # how fast should the toolhead move to release the hold of the magnets after docking					   
variable_z_drop_speed:          20    # how fast the z will lower when moving to the z location to clear the probe
variable_home_z_height:         10    # Z when homing

# if a separate Z endstop switch is in
# use, specify the coordinates of the switch here (Voron).
# Set to 0 to have the probe move to center of bed
variable_z_endstop_x:            0
variable_z_endstop_y:            0

# location to park the toolhead
variable_park_toolhead:         True  # Enable toolhead parking
variable_parkposition_x:        155
variable_parkposition_y:        155
variable_parkposition_z:        30

#dock location
variable_docklocation_x:        11    # X Dock position
variable_docklocation_y:        158    # Y Dock position
variable_docklocation_z:        5    # Z dock position
variable_dockarmslenght:        60    # Dock arms lenght, toolhead movement necessary to clear the dock arms

#Umbilical to help untangle the umbilical in difficult situations
variable_umbilical_x:           75    #X umbilical position
variable_umbilical_y:           225   #Y umbilical position
variable_umbilical:             False #should we untangle the umbilical																   

# Do not modify below
gcode:
    {% set Mx = printer['configfile'].config["stepper_x"]["position_max"]|float %}
    {% set My = printer['configfile'].config["stepper_y"]["position_max"]|float %}
    {% set Ox = printer['configfile'].config["probe"]["x_offset"]|float %}
    {% set Oy = printer['configfile'].config["probe"]["y_offset"]|float %}
    {% set Oz = printer['configfile'].config["probe"]["z_offset"]|float %}

    # if docklocation_z is zero, use Home Z height for safety
    {% if docklocation_z == 0 %}
        SET_GCODE_VARIABLE MACRO=Probe_Variables VARIABLE=docklocation_z VALUE={ home_z_height }
    {% endif %}

    # If x, y coordinates are set for z endstop, assign them
    {% if z_endstop_x != 0 or z_endstop_y != 0 %}
        SET_GCODE_VARIABLE MACRO=Probe_Variables VARIABLE=z_endstop_x VALUE={ z_endstop_x }
        SET_GCODE_VARIABLE MACRO=Probe_Variables VARIABLE=z_endstop_y VALUE={ z_endstop_y }

    # if no x, y coordinates for z endstop, assume probe is endstop and move toolhead to center of bed
    {% else %}
        SET_GCODE_VARIABLE MACRO=Probe_Variables VARIABLE=z_endstop_x VALUE={ (Mx * 0.5) - Ox }
        SET_GCODE_VARIABLE MACRO=Probe_Variables VARIABLE=z_endstop_y VALUE={ (My * 0.5) - Oy }
    {% endif %}


[gcode_macro Probe_Variables]
variable_probe_attached:            False
variable_probe_state:               False
variable_probe_lock:                False
variable_z_endstop_x:               0
variable_z_endstop_y:               0
gcode:


[gcode_macro Homing_Variables]
default_parameter_reset:            0
gcode:
    {% set R  = params.RESET %}

     {% if R %}
        SET_GCODE_VARIABLE MACRO=Probe_Variables VARIABLE=probe_lock VALUE={ False }
   {% endif %}

# Attach probe and lock it
[gcode_macro Attach_Probe_Lock]
gcode:
    Attach_Probe
    SET_GCODE_VARIABLE MACRO=Probe_Variables VARIABLE=probe_lock VALUE={ True }

# Attach probe and lock it
[gcode_macro Dock_Probe_Unlock]
gcode:
    SET_GCODE_VARIABLE MACRO=Probe_Variables VARIABLE=probe_lock VALUE={ False }
    Dock_Probe

# Attach Probe Routine
[gcode_macro Attach_Probe]
gcode:
    # Get probe attach status
    {% set P = printer["gcode_macro Probe_Variables"].probe_attached %}
    {% set L = printer["gcode_macro Probe_Variables"].probe_lock %}
    {% set V = printer["gcode_macro User_Variables"].verbose %}
    # Get Docking location
    {% set Dx = printer["gcode_macro User_Variables"].docklocation_x %}
    {% set Dy = printer["gcode_macro User_Variables"].docklocation_y %}
    {% set Dz = printer["gcode_macro User_Variables"].docklocation_z %}
    {% set Da = printer["gcode_macro User_Variables"].dockarmslenght %}
    # Safe Z for travel
    {% set Hzh = printer["gcode_macro User_Variables"].home_z_height|float %}
    #Set speed
    {% set St = printer["gcode_macro User_Variables"].travel_speed * 60    %}

    M400 # mandatory to save the new safe position
    #allows the docking position to be independent of the Z offset, necessary for bed mounted probes
    SAVE_GCODE_STATE name=_attachProbe
    SET_GCODE_OFFSET Z=0

    # if x and y are not homed
    {% if not 'xy' in printer.toolhead.homed_axes %}
        { action_raise_error("Must Home X and Y Axis First!") }

    # If probe not attached and locked
    {% elif not P and not L %}
        {% if V %}
            { action_respond_info("Attaching Probe") }
        {% endif %}
        G90

        {% if (not 'z' in printer.toolhead.homed_axes) %}
            {% if V %}
                { action_respond_info("Resetting Z position to zero") }
            {% endif %}
            SET_KINEMATIC_POSITION Z=0
        {% endif %}

        {% if (printer.toolhead.position.z < Hzh) %}
            G1 Z{Hzh} F1200
        {% endif %}													 
	Umbilical_Path													 

        # Probe entry location
        G1 X{Dx} Y{Dy|int - Da|int} F{St}
        # pickup from Probe location
        G1 X{Dx} Y{Dy} F1800
        # Probe entry location
        G1 X{Dx} Y{Dy|int - Da|int} F6000

        Park_Toolhead

        CheckProbe action=attach

        {% elif L %}
            {% if V %}
                { action_respond_info("Probe locked!") }
            {% endif %}

            # Probe attached, do nothing
            CheckProbe action=query

        {% else %}
            {% if V %}
                { action_respond_info("Probe already attached!") }
            {% endif %}
        {% endif %}

        # Probe attached, do nothing
        CheckProbe action=query
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

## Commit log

2021-09-22 Isolated Gantry
    B Idler Created
    Imported Micron X Axis
    Corrected X Axis Alignment
    Belts Extended to 120mm bed lengths
    Gantry Belt Path Alignment Tweaked
    Added SaladFork Logo to Toolhead & Idlers
2021-09-22 Added cuts to XY Joints for MGN9 rail
2021-09-23 MakerBeam Updates
    Updated Profiles to MakerBeam
    Revised bodies to accept MB profiles
    [MakerBeam1515.stp]
2021-10-17 Dishwasher Nozzle Brush & Purge Bucket
    [Dishwasher_Assy v4.step, Dishwasher_Brush_Holder_x1.stl, Dishwasher_Bucket_x1.stl]
2021-10-17 Panel DXFs
    [ACM_DECK_WHITE_x1.dxf, ACM_REAR_WHITE_x1.dxf, ACRYLIC_FRONT_CLEAR_x1.dxf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]
2021-10-17 Config Dump
    [DisplayEncoder.cfg, TMC2209.cfg, klicky_sf.cfg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]
2021-10-18 Salad Fork Screwed Fan Mounts
    [Fan_Support_Screwed.step, Fan_Support_Screwed.stl]
2021-10-24 Updated CAD Model
2021-10-24 Create Dishwasher_Brush_Holder+8mmHD.stl
    8mm Lower Mount for Home Depot brass brushes
    [Dishwasher_Brush_Holder+8mmHD.stl]
2021-10-24 LightBar creation
    [LightBar_135A_v1.stl, LightBar_135B_v1.stl, LightBar_150A_v1.stl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]
2021-11-08 Initial Commit
    Kepler Tool Head - WIP
    [Carriage_Kepler_v19.stl, Kepler_HotEnd_v10.stl, Kepler_Strain_Relief_v3.stl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]
2021-11-08 BOM additions
2021-11-16 Alternate Bucket
    This bucket extends to just short of the brush tip to help with knocking off the purge feed so that it doesn't drag along the brush and get caught. The bucket width is also increased to offer easier emptying and less clog risk when waiting multiple prints between emptying.
    [Dishwasher_Bucket_Taller_v1.stl]
2021-12-24 Salad Spinner 1st Commit
    Initial commit of the Salad Spinner Horizontal Spool Holder
    [Spinner_BowdenBPST.stl, Spinner_BowdenGuide.stl, Spinner_Clamp.stl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]
2021-12-29 Added photos & thin clamp, updated Readme.md
    [Spinner_Clamp_Thin.stl]
2022-01-07 Added CAD files
    Exported STEP files for Salad Spinner Components
    [Spinner_Clamp_LgSpool.step, Spinner_Clamp_Standard.step, Spinner_Clamp_Thin.step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]
2022-01-07 Added Photos
    Photos of the Salad Spinner mounted to the Fork
2022-04-20 Add files via upload
    Additional version for 7.1mm OD heatserts
    [Filament_Spinner_7.1ODInserts.step]
2022-04-20 Add files via upload
    Additional STL for 7.1mm OD heatserts
    [Spinner_Core_7.1ODInserts.stl]
